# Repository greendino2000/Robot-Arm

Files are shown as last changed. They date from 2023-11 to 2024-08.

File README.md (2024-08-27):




# Robot Arm

An affordable and opensource 4 DoF desktop robot arm powered by Arduino



## Features

#### Arm
- Fully 3D printed body
- Low-cost design
- Easy repairability
- Built-in and easy-to-program routines
- Controllable over serial from any device
    - Allows for easy integration with custom-made software



#### Web UI ([Link](https://armcontrol.greendino.dev/))
- Interactive terminal
- Full control of the arm's movement
    - Individual control of each motor and servo
        - Slider control & Text boxes
    - Direct serial control through terminal
        - Reference "Manual Control"
- Added routine functionality
    - Easy programming of routines
    - Integrated execution of routines without the need to hardcode the routines to the Arduino
    - Intelligent file parsing for quick routine sharing between users and devices




## Control Methods

### Manual Control
Manual commands can be sent directly to the Arduino using the serial tool.

It is possible (and probably easy) to send the commands using serial tools other than the Arduino IDE, but I haven't gotten to it.

| Axis Name | Identifier | Usage (Identifier + Angle) |
| - | - | - |
| Base | `A` | A180 |
| First arm segment | `B` | B90 |
| Second arm segment | `C` | C90 |
| Claw open/close | `D` | D85 (open) / D150 (closed)* |
| Claw joint | `E` | E90 |

**It is important not to go outside the range provided for the claw, otherwise, it will break the servo.*

### Routines
*The following routines come built-in with the arm's firmware.*

| Routine Name | Identifier | Usage |  |
| - | - | - | - |
| Vertical | `1` | 1 | Routine 1 Gif |
| 90° Rotation Grab | `2` | 2 | Routine 2 Gif |

## BOM

#### Electronics

| Part | Count |
| - | - |
| [TB6612 Stepper control board](https://www.adafruit.com/product/2448) | `1` |
| [DC barrel jack](https://www.adafruit.com/product/373) | `1` |
| [Servo extension cable](https://www.adafruit.com/product/972) | `3` |
| [Power Switch](https://www.adafruit.com/product/482) | `1` |

| Part | Torque | Count |
| - | - | - |
| [MG996R Servos](https://a.co/d/dw7dRt2) | 12kg/cm | `1` |
| [SG90 Servos](https://a.co/d/6B0u2jD) | 1kg/cm | `1` |
| [Nema 17 Stepper Motor](https://a.co/d/1J1Ycyb) | 13Ncm | `1` |

#### Hardware

| Part | Size | Count |
| - | - | - |
| [Rigid Flange Shaft Coupling](https://a.co/d/5UAfUNy) | 5 mm | `1` |
| [M4 Screw Kit](https://a.co/d/59BZscf) | 4 mm | `1` |
| [M3 Screw Kit](https://a.co/d/ajKkV96) | 3 mm | `1` |
| [M1 Screw Kit](https://a.co/d/dh6dXQ9) | 1 mm | `1` |
| [Servo Horns for MG996R](https://a.co/d/1S2e7fp) | 3 mm | `1` |

#### 3D Printed Parts

| File Name | Infill | Supports | Count |
| - | - | - | - |
| BaseSwivel | 75% | ❌ | `1` |
| Base | 20% | ❌ | `1` |
| SmallServoBigHornArmSegment | 20% | ❌ | `1` |
| BigServoArmSegment | 20% | ❌ | `1` |
| ClawJoint | 20% | ❌ | `1` |
| Electronics Enclosure Top | 40% | ❌ | `1` |
| Electronics Enclosure Shell | 20% | ❌ | `1` |

***Note:** "Count" refers to the number of times the linked product should be purchased. A more specific count for items such as screws and servos will be available with the build guide. The linked items generally come in a larger quanitity than needed.*

*The URLs provided link to the actual parts and sites that I purchased and used for this project. These parts can be substituted. This list is being updated as updates are made. I do not make any commission from these links*

## To-do

#### Arm

- Add limit switch to base to determine 0 automatically.
    - Currently, the base sets the position it is in on startup as 0.

#### Other

- Add tutorial on how to upload code to Arduino

- Create step-by-step assembly guide

- Update BOM

- Upload photos of newest iteration of robot arm

<details>
<summary>Archived</summary>
<br>

#### Arm

- ✅ Redesign the entire arm to support larger/higher torque servos.
    - ✅ This will increase the cost, so this will only happen once there is a working version using the affordable micro servos so this project can be viable for people who want to build their own robot arm for less.
 
      

- ✅ Determine solution for hot stepper motor shaft melting base slot, resulting in unstable arm.
    - **Solution:** Added flange shaft coupling to stepper motor shaft to better secure the arm to the base and disperse heat. Need to lower the stepper motor into the electronics box to compensate for the height of the coupler.
 
      

- ✅⭐ Remove the DC barrel jack from the circuit board
    - Replace with a [panel mount](https://www.adafruit.com/product/610) design that will run wires to a header
      
      

- ✅ Add a USB keystone to the electronics box
    - Determine if a USB-A to USB-B keystone would work
 
      

#### App

- ✅ Update control software to support the new arm code.

- ✅ Add the ability to save the current position as movement points for a routine.

- ✅ Add the ability to select end effectors (claw, pen holder, etc.)

#### Other

- ✅ Create a web app for simulation and programming without the physical arm
    - *Kinda need to learn how to do that first though*

</details>

## Gallery
<details>
<summary>V0</summary>
<br>
</details>
<details>
<summary>V1</summary>
<br>
    
</details>
<details>
<summary>V2</summary>
<br>
    
</details>
<details>
<summary>Presentation</summary>
<br>
    
</details>

## FAQ

**Q:** I'm having a hard time building this for myself. Can I reach out for help?

**A:** For sure! Send me an email and I'll be happy to guide you through building and operating your new robot arm.

---

**Q:** Where is the part list for the arm design that uses only micro servos?

**A:** The part list for the initial design that only used micro servos will be available once I finish the build guide for that specific version.

---

## Credits

- Author: [William Heald | @greendino2000](https://www.github.com/greendino2000)

## Contact

If you have any feedback or questions, please reach out to me at greendino30ba@gmail.com

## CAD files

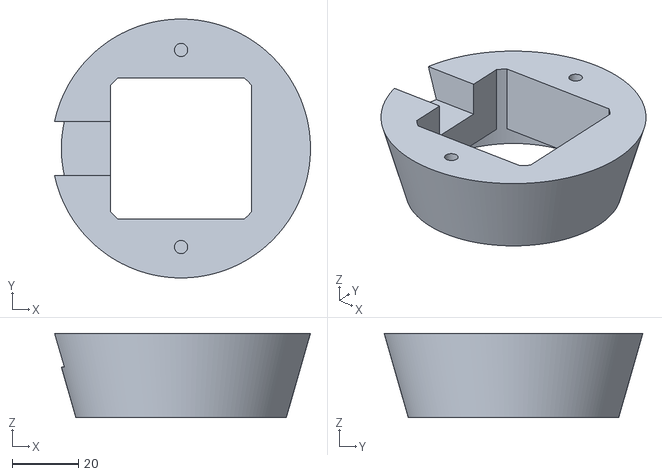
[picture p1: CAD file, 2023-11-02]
Model STLs/Base.stl
77.2 x 78.1 x 25.4

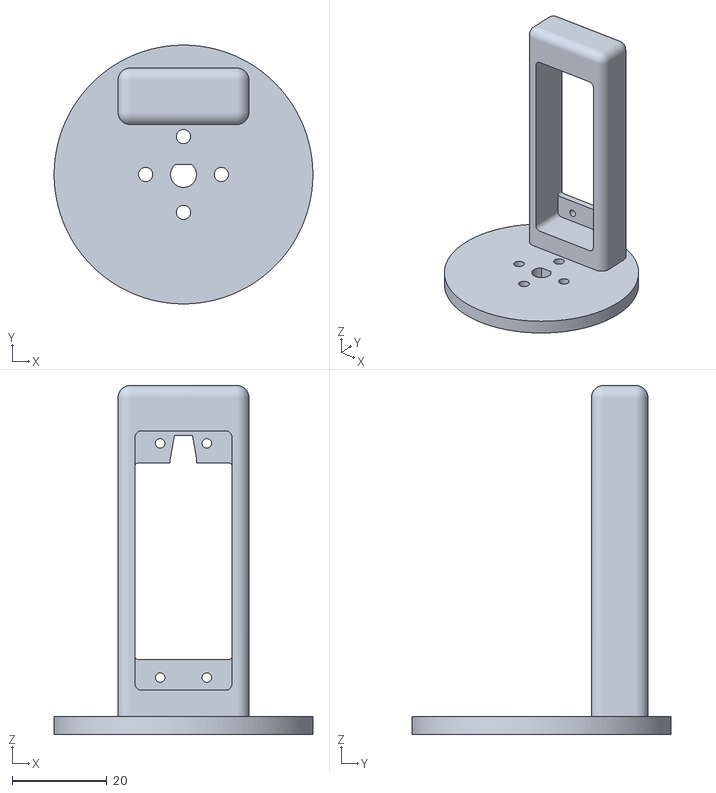
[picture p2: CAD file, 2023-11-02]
Model STLs/BaseSwivel.stl
54.6 x 54.6 x 73.7

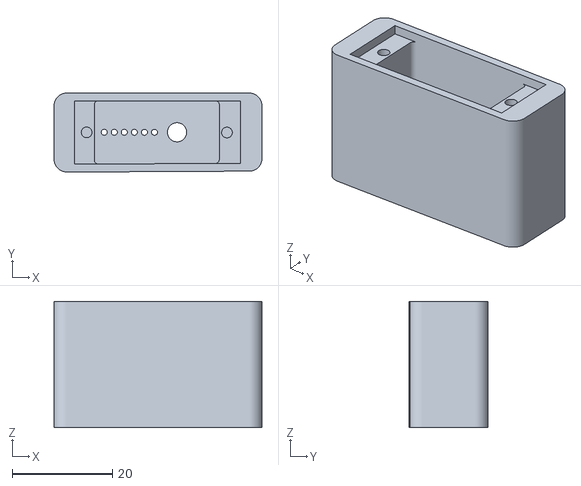
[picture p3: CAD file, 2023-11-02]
Model STLs/ClawJoint.stl
41.4 x 15.7 x 25.1

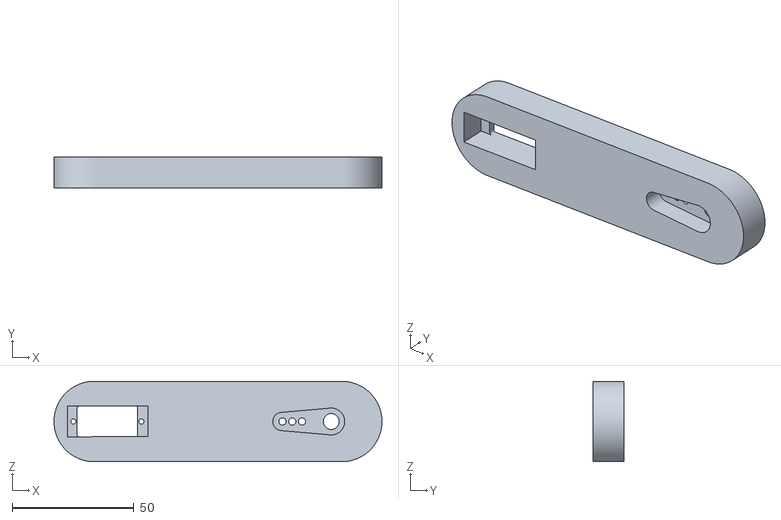
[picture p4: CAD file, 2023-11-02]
Model STLs/SmallServoBigHornArmSegment.stl
134.6 x 12.7 x 33.0

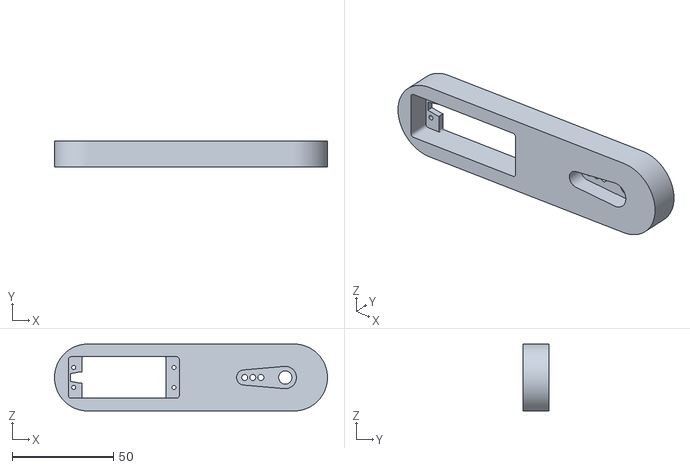
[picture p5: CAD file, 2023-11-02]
Model STLs/BigServoArmSegment.stl
134.6 x 12.7 x 33.0

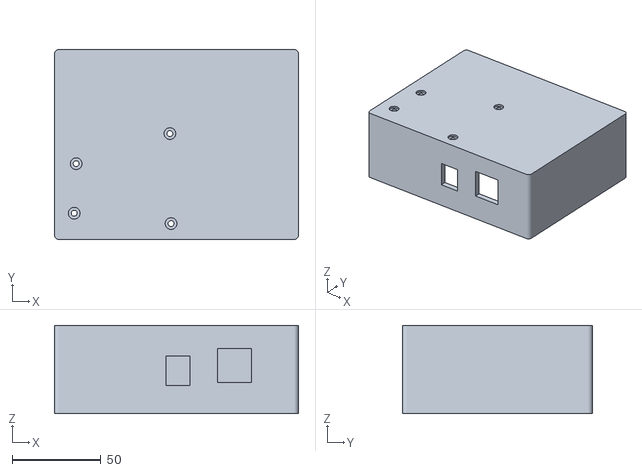
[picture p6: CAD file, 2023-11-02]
Model STLs/Electronics Enclosure Shell.stl
137.2 x 106.8 x 49.5

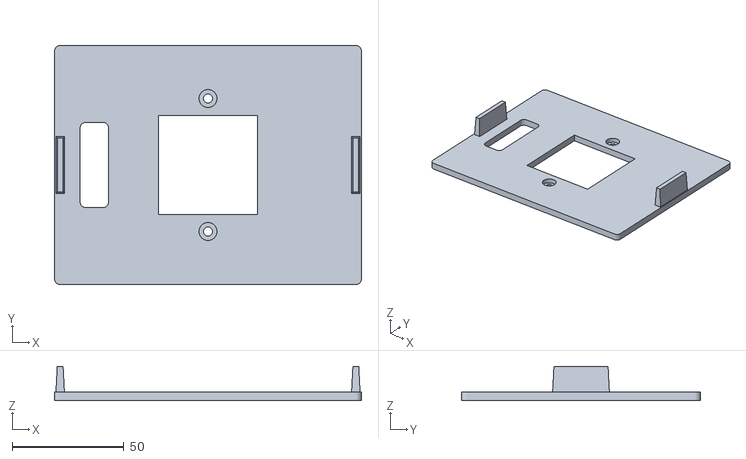
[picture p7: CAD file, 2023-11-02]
Model STLs/Electronics Enclosure Top.stl
137.2 x 106.8 x 15.2

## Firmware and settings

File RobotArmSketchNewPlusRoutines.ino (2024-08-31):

#include <AccelStepper.h>
#include "ServoEasing.hpp"

// Stepper motor pins
#define MOTOR_PIN_1 8
#define MOTOR_PIN_2 9
#define MOTOR_PIN_3 10
#define MOTOR_PIN_4 11

// First arm segment servo
#define SERVO1_PIN 4
// Second arm segment servo
#define SERVO2_PIN 5
// Claw joint rotation servo
#define SERVO3_PIN 6
// Claw open/close servo
#define SERVO4_PIN 7

#define STEPS_PER_REVOLUTION 200
#define NUM_SERVOS 4

int delayTime = 1000;

AccelStepper stepper(AccelStepper::FULL4WIRE, MOTOR_PIN_1, MOTOR_PIN_2, MOTOR_PIN_3, MOTOR_PIN_4);
ServoEasing servos[NUM_SERVOS];

// Define RoutineStep structure
struct RoutineStep {
  int stepperPosition;
  int servoPositions[NUM_SERVOS];
};

// Define routines
RoutineStep routine1[] = { // Vertical
  {1, {90, 0, 100, 90}},
};

RoutineStep routine2[] = { // 90 deg grab
  {0, {140, 140, 100, 90}},
  {0, {20, 65, 55, 130}},
  {0, {20, 65, 55, 80}},
  {0, {140, 140, 100, 80}},
  {50, {20, 55, 55, 80}},
  {50, {20, 55, 55, 130}},
  {50, {140, 130, 100, 90}},
  {0, {90, 0, 100, 90}},
};

RoutineStep routine3[] = { // Fold
  {0, {140, 140, 100, 90}},
};

RoutineStep routine4[] = { // 90 deg grab adjusted
  {0, {140, 140, 100, 90}},
  {0, {5, 55, 50, 130}},
  {0, {5, 55, 50, 75}},
  {0, {140, 140, 100, 75}},
  {50, {5, 55, 50, 75}},
  {50, {5, 55, 50, 130}},
  {50, {140, 130, 100, 90}},
  {0, {90, 0, 100, 90}},
};

void setup() {
  Serial.begin(9600);
  
  stepper.setMaxSpeed(250);
  stepper.setAcceleration(125);
  stepper.setCurrentPosition(0);

  // Attach servos to pins
  servos[0].attach(SERVO1_PIN);
  servos[1].attach(SERVO2_PIN);
  servos[2].attach(SERVO3_PIN);
  servos[3].attach(SERVO4_PIN);

  // Set default servo speed
  setSpeedForAllServos(180);

  // Move to upright position
  executeRoutine(routine1, sizeof(routine1) / sizeof(routine1[0]));
}

/**
 * Moves the stepper motor to the specified target position.
 * If the target position is greater than 200, it sets the target position to 200.
 * Blocks until the motor reaches the target position.
 * Prints the current position of the motor to the serial monitor.
 *
 * @param targetPosition The target position to move the stepper motor to.
 */
void moveStepperToPosition(int targetPosition) {
  if (targetPosition > 200) {targetPosition = 200;}
  stepper.moveTo(targetPosition);
  while (stepper.isRunning()) {
    stepper.run();
  }
  Serial.print("Current Position: ");
  Serial.println(stepper.currentPosition());
}

/**
 * Sets the position of a servo.
 * 
 * @param servoIndex The index of the servo motor to set the position for.
 * @param position The position to set the servo motor to.
 */
void setServoPosition(int servoIndex, int position) {
  if (position >= 0 && position <= 180) {
    servos[servoIndex].easeTo(position);
    Serial.print("Servo ");
    Serial.print(servoIndex + 1);
    Serial.print(" Position: ");
    Serial.println(position);
  }
  else {
    Serial.println("Invalid servo position");
  }
}

/**
 * Executes a routine by moving the stepper motor to the specified position and interpolating the servo positions.
 * @param routine An array of RoutineStep objects that define the positions of the stepper motor and servos for each step of the routine.
 * @param numSteps The number of steps in the routine.
 */
void executeRoutine(RoutineStep *routine, int numSteps) {
  for (int step = 0; step < numSteps; step++) {
    moveStepperToPosition(routine[step].stepperPosition);
    
    // Set target positions for all servos
    for (int servoIndex = 0; servoIndex < NUM_SERVOS; servoIndex++) {
      servos[servoIndex].setEaseTo(routine[step].servoPositions[servoIndex]);
    }
    
    // Start and synchronize all servo movements
    synchronizeAllServosStartAndWaitForAllServosToStop();
    
    delay(delayTime); // Delay between steps
  }
}



/**
 * This function reads serial input and performs actions based on the received character.
 * The function reads the character and an integer value from the serial port and performs the following actions:
 * - 'A': Moves the stepper motor to the specified position.
 * - 'B': Sets the position of servo 0 to the specified value.
 * - 'C': Sets the position of servo 1 to the specified value.
 * - 'D': Sets the position of servo 2 to the specified value.
 * - 'E': Sets the position of servo 3 to the specified value.
 * - '1': Executes routine 1.
 * - '2': Executes routine 2.
 * If an unknown command is received, it is ignored.
 */
void processSerialInput() {
  while (Serial.available()) {
    char receivedChar = Serial.read();
    int value = Serial.parseInt();
    
    switch (receivedChar) {
      // Individual motor control
      case 'A':
        moveStepperToPosition(value);
        break;
      case 'B':
        setServoPosition(0, value);
        break;
      case 'C':
        setServoPosition(1, value);
        break;
      case 'D':
        if(isUpperCase(receivedChar)) {
          setServoPosition(2, value);
        }
        break;
      case 'E':
        setServoPosition(3, value);
        break;
      // WebUI Functions
      case 's': // Set speed
        setSpeedForAllServos(value);
        Serial.print("Speed set to: ");
        Serial.println(value);
        break;
      case 'd': // Set delay
        if(!isUpperCase(receivedChar)) {
          delayTime = value;
          Serial.print("Step delay set to: ");
          Serial.println(value);
        }
        break;
      // Hardcoded routines
      case '1': // Execute routine 1
        executeRoutine(routine1, sizeof(routine1) / sizeof(routine1[0]));
        break;
      case '2': // Execute routine 2
        executeRoutine(routine2, sizeof(routine2) / sizeof(routine2[0]));
        break;
      case '3': // Execute routine 3
        executeRoutine(routine3, sizeof(routine3) / sizeof(routine3[0]));
        break;
      case '4': // Execute routine 4
        executeRoutine(routine4, sizeof(routine4) / sizeof(routine4[0]));
        break;
      // Fallback
      default:
        // Handle unknown command
        break;
    }
  }
}

void loop() {
  processSerialInput();
}

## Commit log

2023-10-03 Added Arduino code
    This is the second rewrite of the control script.
2023-10-14 Updated RobotArmSketchNewPlusRoutines
    - New comments with params for functions
    - Fixed interpolation steps count
    - Reversed claw open/close servo and claw joint rotation servo pins
    [RobotArmSketchNewPlusRoutines.ino]
2023-11-02 Added Robot arm stls to the parts list
2023-11-02 Uploaded the stl files to the repo
    [Base.stl, BaseSwivel.stl, BigServoArmSegment.stl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]
2023-11-03 Fixed spacing for parts list tables
    arm.greendino.dev wasn't displaying the new tables correctly
2023-11-03 Added detail to first sentence
    Made it clear that this is a 4 DoF arm
2024-08-31 Switched servo library to ServoEasing
    Added check for uppercase and lowercase char entry through serial.
    Added adjustable movement speed.
    Added adjustable step delay.

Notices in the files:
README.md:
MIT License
